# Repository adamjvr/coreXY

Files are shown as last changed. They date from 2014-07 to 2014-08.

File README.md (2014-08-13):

CoreXY 3D Printer
==================

A 3D printer using the CoreXY configuration which is based on jand1122's https://github.com/jand1122/RepRap-XY and zelogik's https://github.com/zelogik/AluXY CoreXY 3D printer. 

All source code is written using OpenSCAD.

Modifications include:
* XY ends for a vertical x-axis
* X-carriage (for vertical x-axis) with belt clamps. Uses 30mm spaced screws for mounting extruder/hotend. 
* 10x2 Trapezoidal leadscrew with flange nut
* M5 frame mounting screws

Updates in latest version:
* Less plastic for motor ends, xy-block and idler ends - 18% less plastic
* Separate motor mounts (remove tensioner bearings). Belts are tensioned by sliding motor mount along t-slot.

Frame Size: 400x400x500

Bill of Materials
==================

*Note: This list is only a rough guide and there may be some inconsistencies due to various changes over time.*

**Frame - 20x20 aluminium extrusions (t-slot or v-slot)**
* 4x 500mm length
* 12x 360mm length
* Lots and lots of t-nuts 
* Fittings for corners (i.e. hidden 90deg bracket, brackets, printed brackets)
* Some drop-in t-nuts (for adding parts after frame is assembled)
* ??x M5 button cap bolt

**Z-axis**
* 2x 12mm smooth rod
* 1x Trapezoidal leadscrew (10mm diameter with 2mm pitch)
* 1x 5x10mm rigid coupler 
* 1x 10X2 flanged trapezoidal bronze nut
* 1x 6300Z bearing 
* 2x LM12LUU linear bearing (12mm "long" bearing) - can also use 4x LM12UU 
* 4x Double t-nut (or use 8 t-nuts)
* 14x 40mm M5 bolt
* 8x 25mm M5 bolt
* 4x 15mm M3 bolt (to attach nema motor)
* 1x NEMA17 Stepper motor

**X & Y axis**
* 2x NEMA17 stepper motors
* 24x F624ZZ flanged bearings
* 2x 330-350mm 8mm diameter smooth rod (y-axis)
* 2x 400mm 8mm diameter smooth rod (x-axis)
* 6x LM8UU 8mm linear bearing 
* Approx. 3-4m GT2 belt 
* 2x 20 tooth GT2 Pulley
* 4x 60mm M4 bolts (for XY block bearings)
* ??x M4 bolts 
* Lots of M4 nuts and washers
* ??x M3 bolts
* 12x 40mm M3 bolts
* 8x 40mm M4 bolts (for idler bearings, screws can be longer)
* ??x M3 nuts and washers
* ??x M5 washers
* ??x M5 nuts
* 8x 25mm M5 bolts
* 6x 55mm M5 bolts
* 4x 30mm M5 bolts
* 6x 15mm M3 bolt 
* 8x 10mm M3 bolt (attach nema motors)

Assembly Notes
==============

* There must be a washer on the outsides of the flange bearings to run smoothly (i.e washer->bearing->bearing->washer). 

* Belt layout diagram:

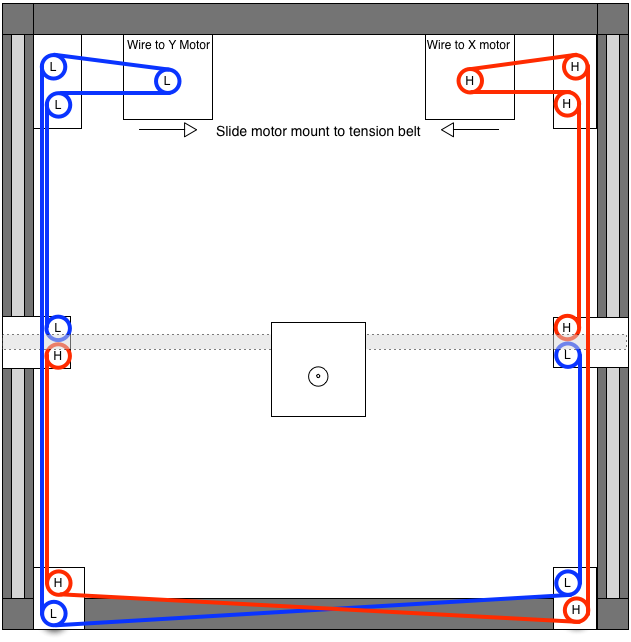
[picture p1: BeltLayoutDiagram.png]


**Notice: This is a work in progress. Use at your own risk!**

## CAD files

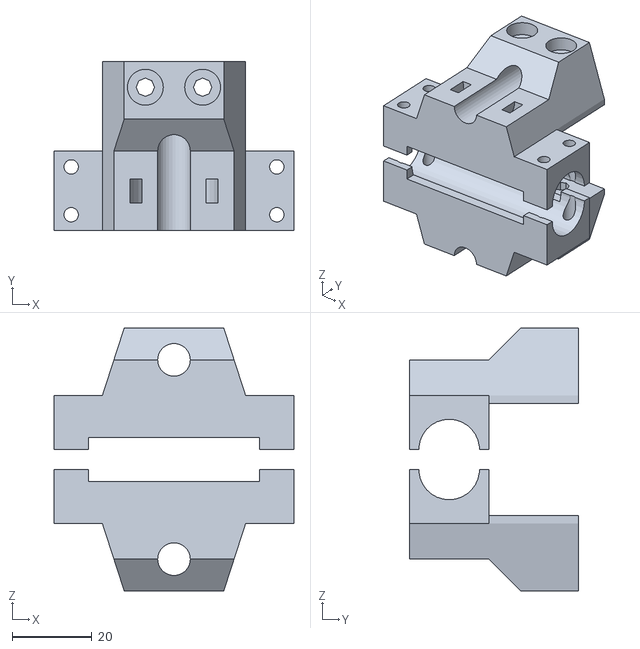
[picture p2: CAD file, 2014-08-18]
stl/xy_block.stl
60.2 x 42.5 x 66.0

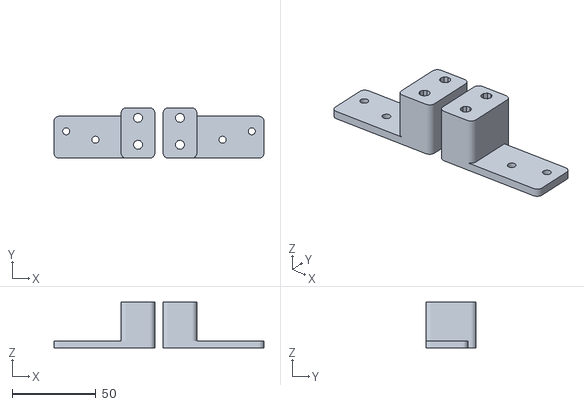
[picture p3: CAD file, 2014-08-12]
stl/y_motor_end_idler_bottoms.stl
125.0 x 30.0 x 27.2

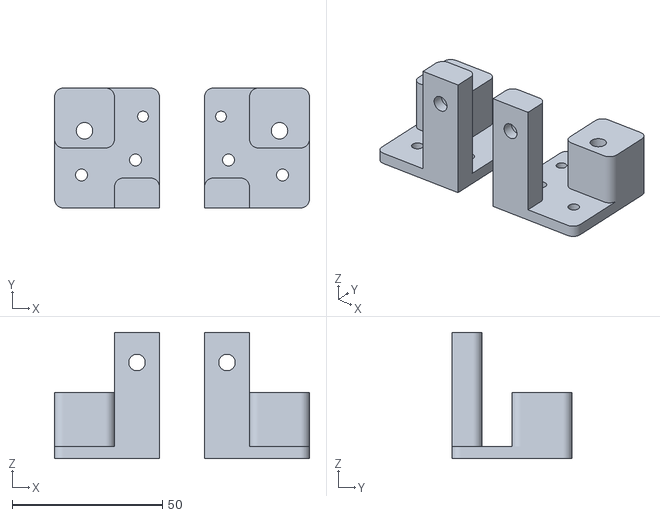
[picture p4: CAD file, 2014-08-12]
stl/y_idler_end_tops.stl
85.0 x 40.0 x 42.0

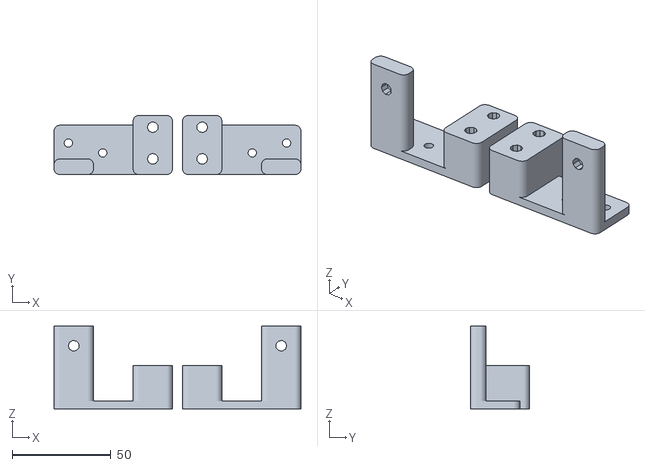
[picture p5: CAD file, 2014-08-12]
stl/y_motor_end_idler_tops.stl
125.0 x 30.0 x 42.0

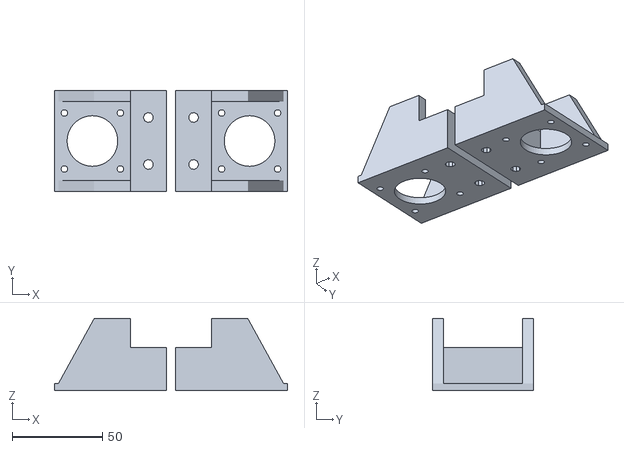
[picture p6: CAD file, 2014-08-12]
stl/y_motor_end_motor_holder.stl
129.0 x 56.0 x 40.0

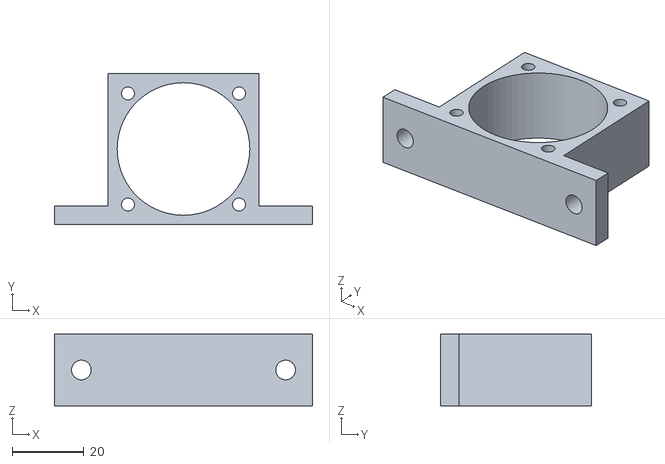
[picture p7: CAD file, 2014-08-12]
stl/bulldog_xl_mount.stl
72.0 x 42.0 x 20.0

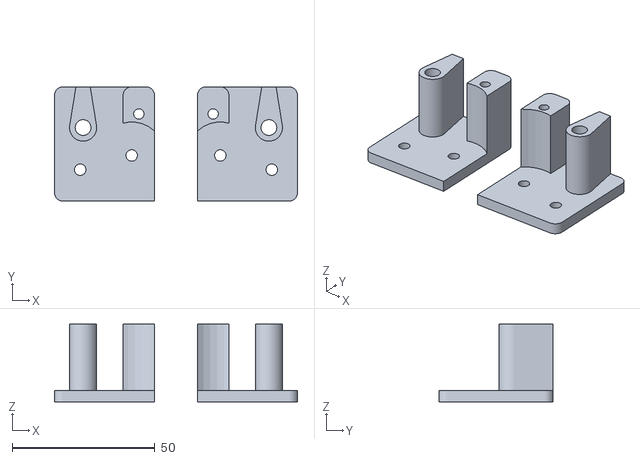
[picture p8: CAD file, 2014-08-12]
stl/y_idler_end_bottoms.stl
85.0 x 40.0 x 27.2

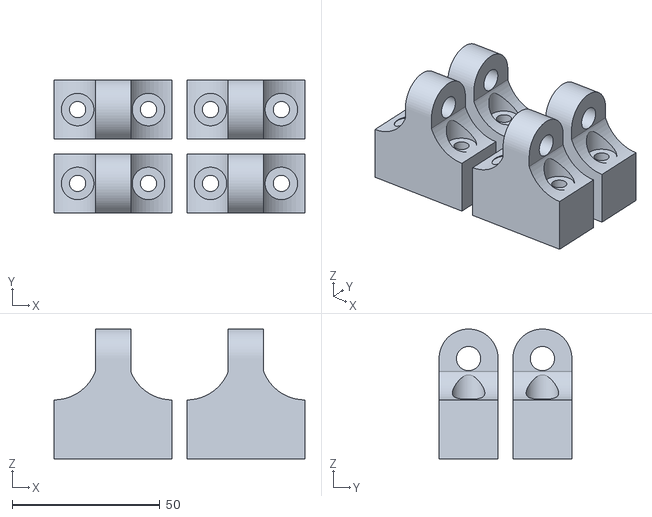
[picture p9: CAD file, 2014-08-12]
stl/y_rod_holders.stl
85.0 x 45.0 x 44.0

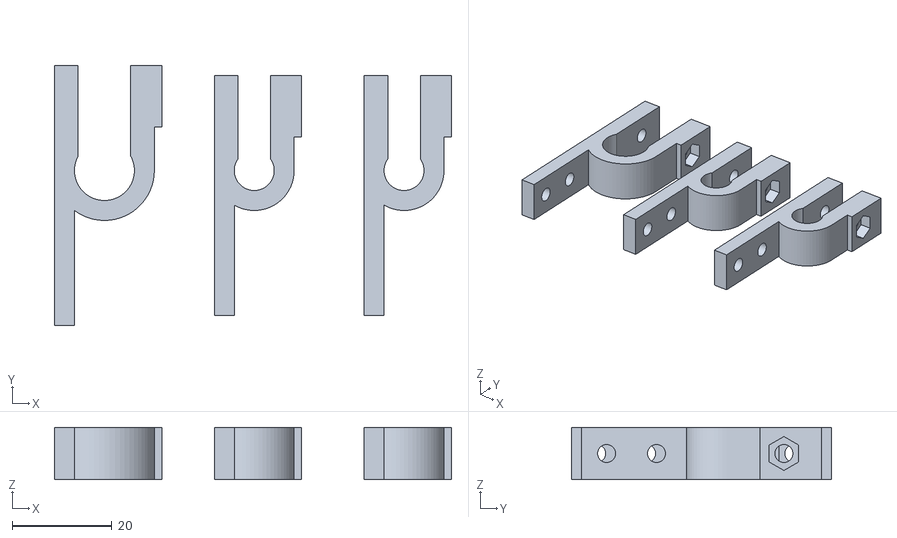
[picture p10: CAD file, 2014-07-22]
stl/endstop_holder.stl
79.5 x 52.0 x 10.5

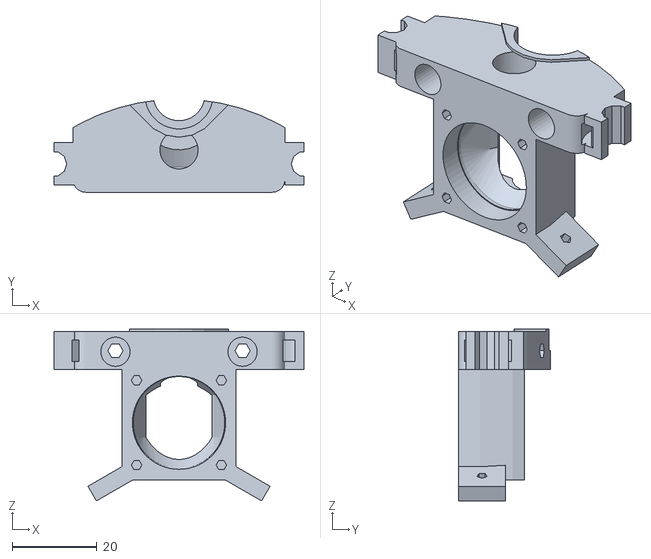
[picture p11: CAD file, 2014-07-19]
stl/jhead_bowden_mount_fan.stl
59.0 x 21.6 x 40.6

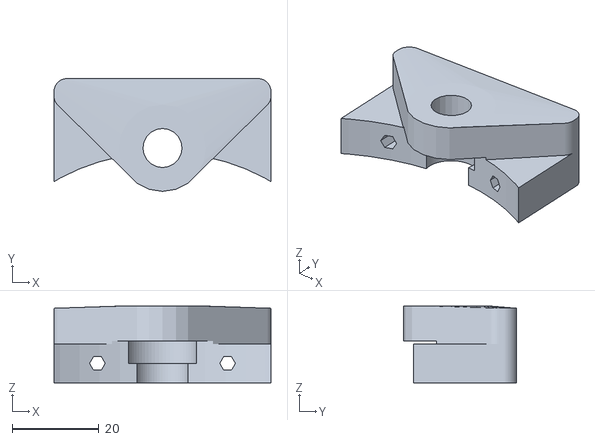
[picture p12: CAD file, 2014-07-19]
stl/jhead_bowden_mount.stl
50.0 x 26.0 x 17.7

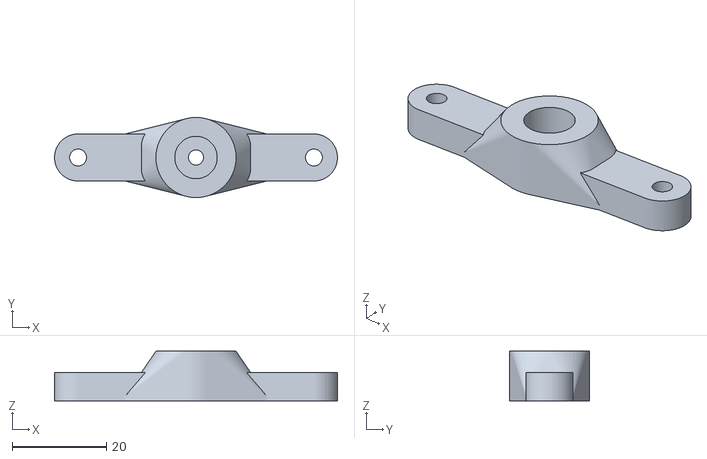
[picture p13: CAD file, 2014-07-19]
stl/i3_gregs_wades_bowden_adapter.stl
60.0 x 17.0 x 10.5

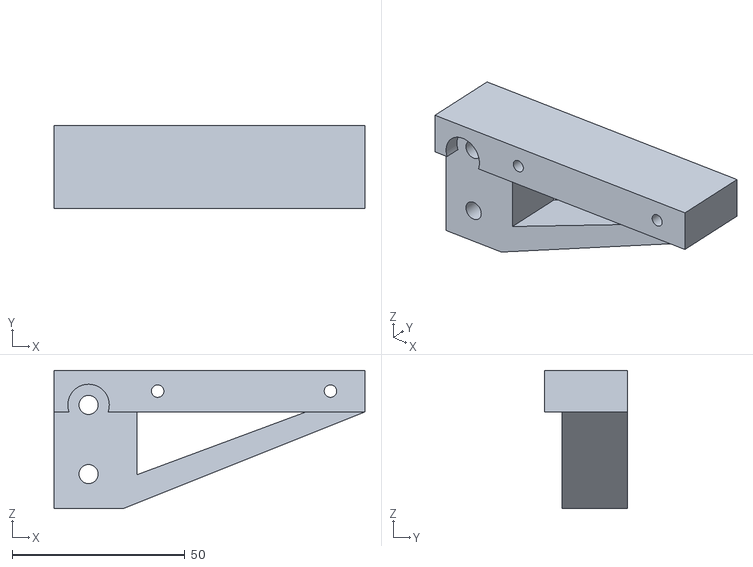
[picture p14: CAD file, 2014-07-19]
stl/i3_gregs_wades_frame_mount.stl
90.0 x 24.0 x 40.0

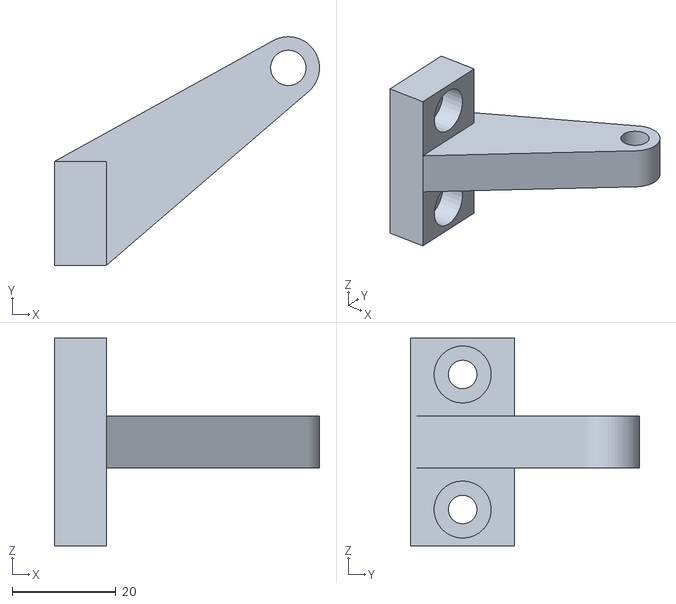
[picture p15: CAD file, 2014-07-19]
stl/i3_gregs_wades_frame_bowden_guide.stl
51.0 x 44.0 x 40.0

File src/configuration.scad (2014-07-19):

// Configuration
// Author: sdavi


include <dimensions.scad>
use <library.scad>


x_rod_distance = 45;

y_bearing = LM8UU;
x_bearing = LM8UU;
z_bearing = LM12LUU;
belt_bearing = BEARING_2x624;


end_belt_bearing_distance = 25;// distance between 2 bearings on y-ends
belt_clearance = 9.5; //space for belts

frame_screw = M5; //m5 screws for v/tslot

frame_spacer_height = 18; //height to spacer to mount to frame to clear x-ends 


// calculated vars

//y bearing block
y_bearing_block_length = 2*y_bearing[2] + M3*2 + 5;
y_bearing_block_width = y_bearing[1]+5;
y_bearing_block_height = 6+y_bearing[1]/2;

xy_bearing_distance = y_bearing_block_width/2+belt_clearance+belt_bearing[1]/2; //distance between center of y-bearing to center of x-belt bearing 


//min height for belt bearings
min_beltbearing_height = max(((belt_bearing[2]+m4_washer_thickness*2) * 2), y_bearing_block_height);

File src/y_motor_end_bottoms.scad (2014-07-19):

// y_motor end
// Author: sdavi

include <lib/y_motor_end.scad>


translate([5,0,0]) y_motor_end_bottom();
mirror([1,0,0])y_motor_end_bottom();

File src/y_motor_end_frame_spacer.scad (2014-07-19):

// y_motor end spacer
// Author: sdavi


include <lib/y_motor_end.scad>

translate([5,0,0])frame_spacer();
mirror([1,0,0])frame_spacer();

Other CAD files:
stl/x_carriage_bowden_guide.stl
stl/z_carriage_outer.stl
stl/z_carriage_inner.stl
stl/z_carriage_outer(mirror).stl
src/y_motor_end_idler_bottoms.scad
src/belt_bearing_spacer.scad
src/bulldog_xl_mount.scad
src/dimensions.scad
src/endstop_holder.scad
src/endstop_holder_rrd_halleffect.scad
src/hotend_mounts/E3D_bowden_hotend_mount.scad
src/hotend_mounts/jhead_bowden_hotend_mount.scad
src/hotend_mounts/jhead_dual_bowden_hotend_mount.scad
src/i3_gregs_wades_mount.scad
src/i3_y_carriage_adapter.scad
src/library.scad
src/x-carriage.scad
src/x-carriage_clamps.scad
src/xy_block.scad
src/y_idler_end_bottoms.scad
src/y_idler_end_tops.scad
src/y_motor_end_idler_tops.scad
src/y_motor_end_motor_holder.scad
src/y_rod_holders.scad
src/z_carriage_inner.scad
src/z_carriage_outer(mirror).scad
src/z_carriage_outer.scad
src/z_ends.scad
src/z_nut_holder.scad
src/z_rod_clamps.scad
stl/belt_bearing_spacer.stl
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

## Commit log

2014-07-19 Added source files
    [E3D_bowden_hotend_mount.scad, belt_bearing_spacer.scad, configuration.scad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]
2014-07-22 Added Endstop holders
    [endstop_holder.scad, endstop_holder.stl, endstop_holder_rrd_halleffect.scad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]
2014-08-12 Revised xy parts
    [bulldog_xl_mount.scad, bulldog_xl_mount.stl, configuration.scad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]
2014-08-13 Updated halleffect holder and readme
    [endstop_holder_rrd_halleffect.scad]
2014-08-18 revert back to 2 bearings for xy block
    [configuration.scad, xy_block.scad, xy_block.stl]
